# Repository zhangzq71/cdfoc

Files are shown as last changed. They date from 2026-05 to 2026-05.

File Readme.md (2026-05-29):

CDFOC Introduction
=======================================

Your browser may not support avif images!

Sockets: RS-485: molex 5264 (4 pin x 2), motor: molex 5264 (3 pin), sensor: sh1.0 (10 pin)

Download this project:
```
git clone --recursive https://github.com/dukelec/cdfoc
```



## Protocol

CDFOC is an open-source Field-Oriented Control (FOC) motor controller that communicates over an RS485 interface.
 - Default baud rate: 115200 bps
 - Maximum speed: 50 Mbps
 - Default address: 0xfe

The underlying protocol is CDBUS, with the following frame format:  
`src, dst, len, [payload], crc_l, crc_h`

Each frame includes a 3-byte header, a variable-length payload, and a 2-byte CRC (identical to Modbus CRC).  
For more information on the CDBUS protocol, please refer to:
 - https://cdbus.org

The payload is encoded using the CDNET protocol. For detailed information, please refer to:
 - https://github.com/dukelec/cdnet
 - https://github.com/dukelec/cdnet/wiki/CDNET-Intro-and-Demo

## Block Diagram



## GUI Tool

CDBUS GUI Tool: https://github.com/dukelec/cdbus_gui

Example: Upon power-on, first write 5 to `state`, then write the target position to `tp_pos` to rotate the motor.



After modifying the configuration, write 1 to `save_conf` to save the configuration to flash.  
If you need to restore the default configuration, change `magic_code` to another value and save it to flash. Then reapply power.

Plots:



## Operating

### Calibration mode (state = 1)

Do not connect any loads to the motor during calibration.

Write 1 to `dbg_en` to enable debug prints in the GUI.

Start by setting the appropriate value for `cali_current`, it is recommended to set the value a little higher to allow the motor to lock more accurately.
Also be careful to prevent the motor from overheating.

Write 1 to `cali_run` to start the calibration. The motor coils will be energized sequentially, causing the motor to turn clockwise first, then counterclockwise.
Afterward, the calculated encoder offset value will be printed and written to `bias_encoder`. Be sure to save it to flash.

Writing 1 to `cali_run` automatically sets `state` to 1.

### Torque Mode (state = 2)

Write 2 to `state` to enter torque mode, or current mode. 

The motor can then be rotated by writing the appropriate current value to `tgt_current`. 

The unit of current is the LSB value of the 12bits ADC. 

### Speed Mode (state = 3)

Write 3 to `state` to enter speed mode.

Then write the appropriate speed value to `tgt_speed` to rotate the motor.

One revolution of the motor is divided into 0x10000 units, e.g. from 0 to 0x10000 is one full revolution.  
The unit of speed is: how many position-units / second.

### Position Mode (state = 5)

Write 5 to `state` to enter position mode.

Then just write the appropriate values to `tp_pos`, `tp_speed`, `tp_accel`.

Alternatively these parameters can be updated using the quick-exchange command by default.

Mode 4 of `state` is a position mode without acceleration or deceleration and is not normally used.

## Command Demonstration

The address of the `state` itself is `0x0240` and its length is 1 byte.
To lock the motor and enter position mode after power up, send the following data to port 5:
```
20  40 02  05
```
`20` is the subcommand `write`, `40 02` is the little-endian for address 0x0240 (little-endian is used unless otherwise noted),
and `05` is the value to be written.

The complete command containing the CRC is (host address defaults to `0`, motor address defaults to `0xfe`, 3rd byte is data length, last two bytes are CRC):

```
00 fe 06  40 05  20  40 02  05  eb 8f
```

The complete response package is:
```
fe 00 03  05 40  00  crc_l crc_h
```

The last `0x00` means no error.

### Quick Exchange Commands

`qxchg_set` uses only one element by default, pointing to the area where the table entries `tp_pos`, `tp_speed` and `tp_accel` are located.  
If you want to change the target position parameter `tp_pos` to 0, you can write data `00 00 00 00` to port 6.  

If you need to change both the target position and the target speed, e.g. position to 0x00010000 and speed to 0x00005000, writes: `00 00 01 00  00 50 00 00`.

Goes to 0 degrees, full command with CRC:
```
00 fe 06  40 06  00 00 00 00  64 f8
```

Goes to 180 degrees, full command with CRC:  
(0x10000 units for one revolution, 0x8000 for 180 degrees)

```
00 fe 06  40 06  00 80 00 00  65 10
```

Rotates to the 5th revolution position and sends the speed value (0x00140000 or 14 revolutions per second) with the CRC:
```
00 fe 0a  40 06  00 00 05 00  00 00 14 00  ae c4
```

Demonstration of return data for the above three commands:
```
fe 00 0a  06 40  xx xx xx xx yy yy yy yy  crc_l crc_h
```

The `xx` and `yy` are defined by `qxchg_ret` to return 8 bytes of data such as `tgt_pos`.

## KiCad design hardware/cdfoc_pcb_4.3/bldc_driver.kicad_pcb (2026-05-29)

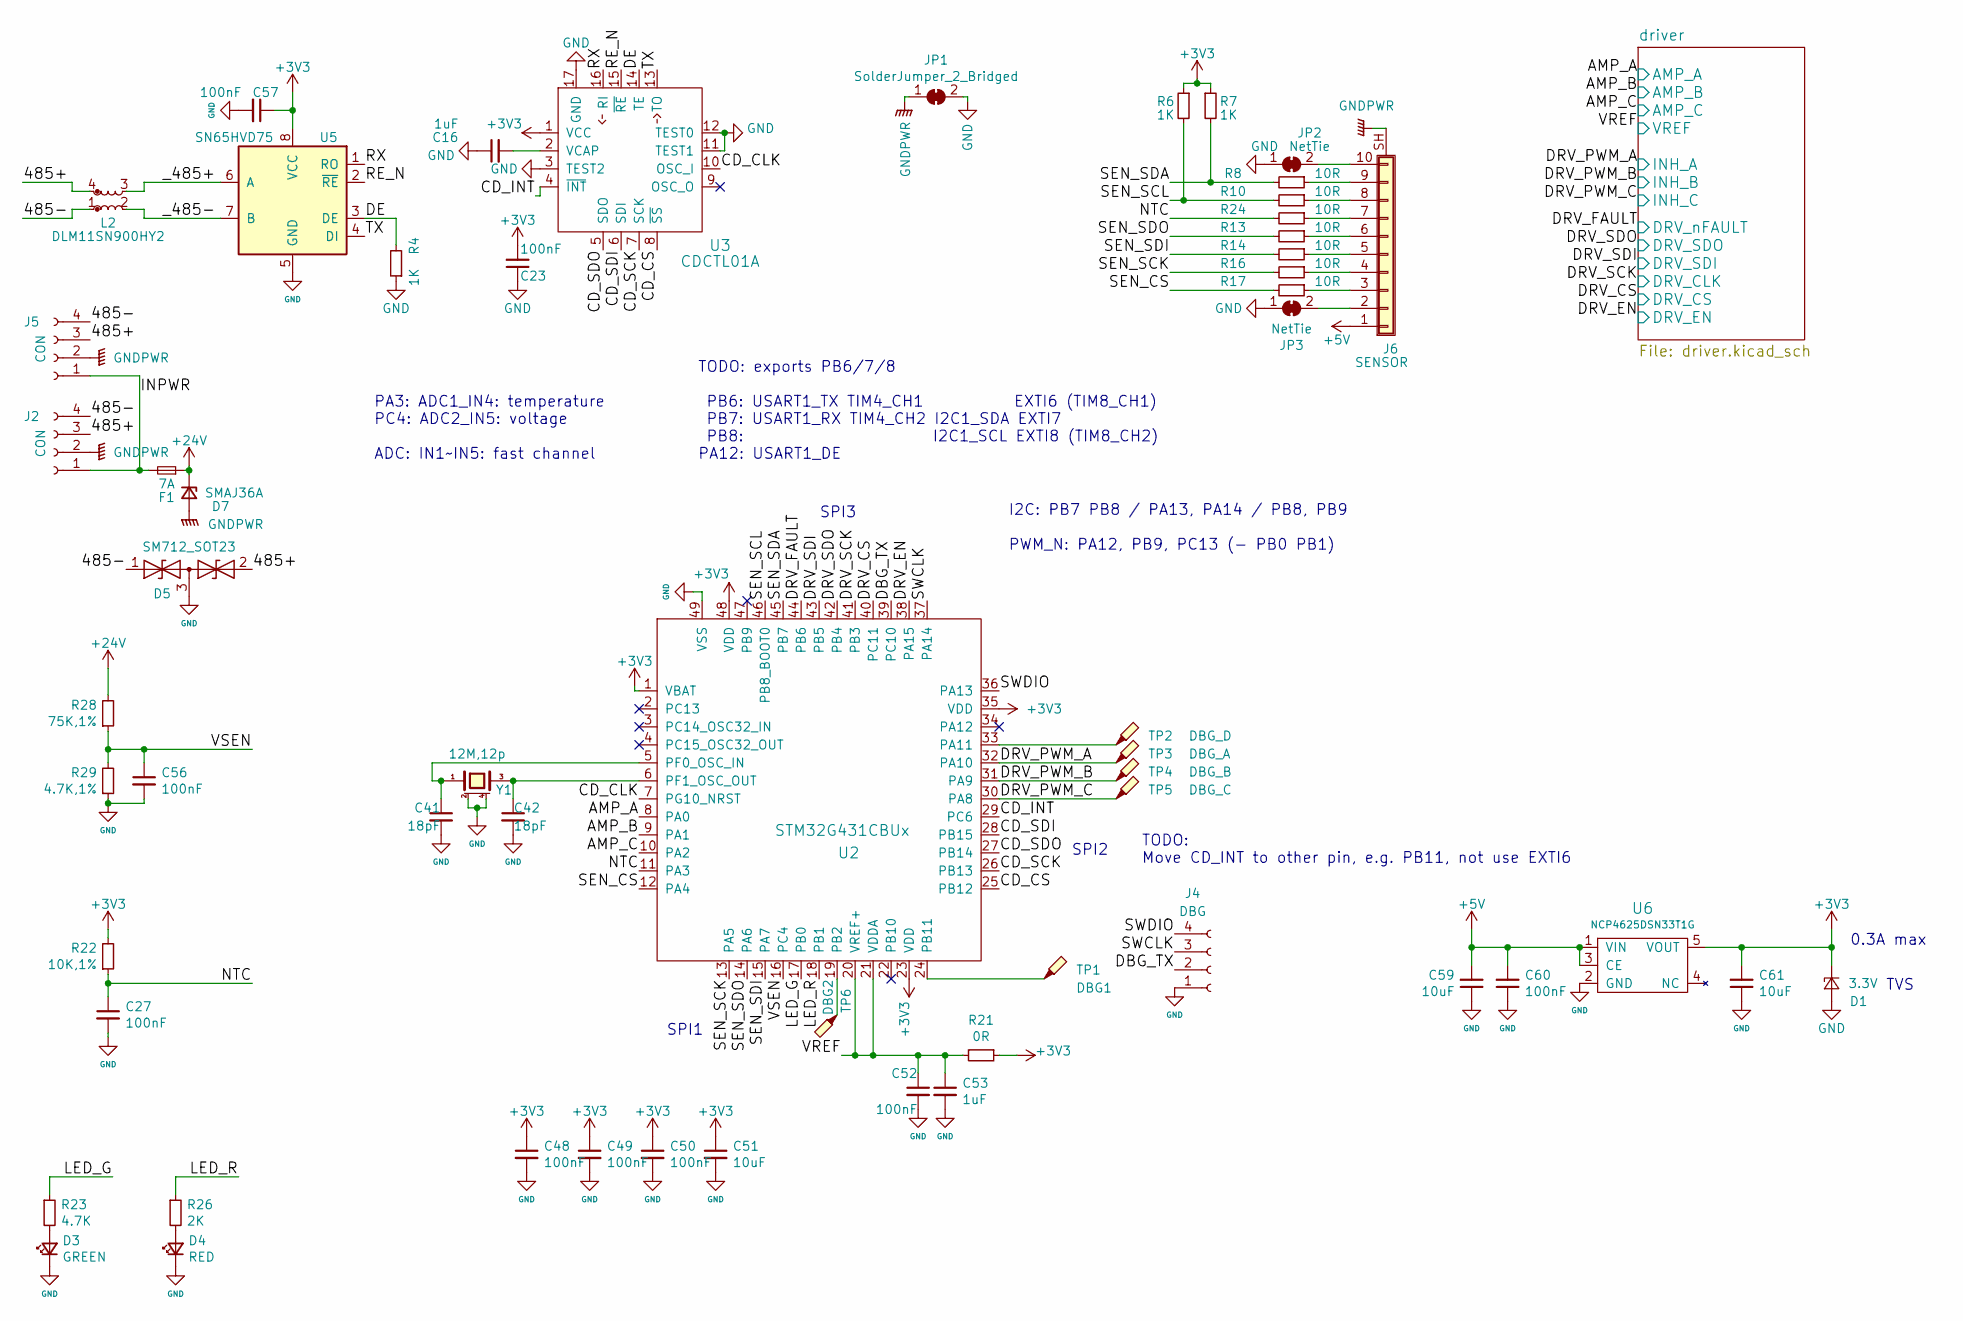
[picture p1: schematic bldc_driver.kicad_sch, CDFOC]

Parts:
C16, C53: 1uF; 0402
C23, C27, C48, C49, C50, C52, C56, C57, C60: 100nF; 0402
C41, C42: 18pF; 0402
C51, C59, C61: 10uF; 0402C_BIG
D1: 3.3V; SOD-923
D3: GREEN; 0402D
D4: RED; 0402D
D5: SM712_SOT23; SOT-23
D7: SMAJ36A; SMA
F1: 7A; 1206R
J2, J5: CON; CONN_5268-04A_1x04_P2.50mm_H
J4: DBG; PAD_DIP_4P_1mm
J6: SENSOR; CONN_SH1.0mm_10P_HSMD
JP1: SolderJumper_2_Bridged; NetTie-2_SMD_Pad1mm
JP2, JP3: NetTie; NetTie-2_SMD_Pad0.5mm
L2: DLM11SN900HY2; L_CommonModeChoke_Coilcraft_0603USB
R4, R6, R7: 1K; 0402
R8, R10, R13, R14, R16, R17, R24: 10R; 0402
R21: 0R; 0402
R22: 10K,1%; 0402
R23: 4.7K; 0402
R26: 2K; 0402
R28: 75K,1%; 0402
R29: 4.7K,1%; 0402
TP1: DBG1; TP-D0.8mm
TP2: DBG_D; TP-D0.8mm
TP3: DBG_A; TP-D0.8mm
TP4: DBG_B; TP-D0.8mm
TP5: DBG_C; TP-D0.8mm
TP6: DBG2; TP-D0.8mm
U2: STM32G431CBUx; QFN-48-1EP_7x7mm_P0.5mm_EP5.6x5.6mm
U3: CDCTL01A; QFN-16-1EP_3x3mm_P0.5mm_EP1.7x1.7mm
U5: SN65HVD75; SON-8
U6: NCP4625DSN33T1G; SOT-23-5
Y1: 12M,12p; XTAL-3225

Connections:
+3V3: C23.2, C48.1, C49.1, C50.1, C51.1, C57.1, C61.2, D1.1 (K), R6.1, R7.1, R21.1, R22.2, U2.1 (VBAT), U2.23 (VDD), U2.35 (VDD), U2.48 (VDD), U3.1 (VCC), U5.8 (VCC), U6.5 (VOUT); also elsewhere on the board
+5V: C59.2, C60.2, J6.1, U6.1 (VIN), U6.3 (CE); also elsewhere on the board
+24V: D7.1 (K), F1.1, R28.2; also elsewhere on the board
/485+: D5.2 (A2), J2.3, J5.3, L2.4
/485-: D5.1 (A1), J2.4, J5.4, L2.1
/AMP_A: U2.8 (PA0); also elsewhere on the board
/AMP_B: U2.9 (PA1); also elsewhere on the board
/AMP_C: U2.10 (PA2); also elsewhere on the board
/CD_CLK: U2.7 (PG10_NRST), U3.10 (OSC_I)
/CD_CS: U2.25 (PB12), U3.8 (~SS)
/CD_INT: U2.29 (PC6), U3.4 (~INT)
/CD_SCK: U2.26 (PB13), U3.7 (SCK)
/CD_SDI: U2.28 (PB15), U3.6 (SDI)
/CD_SDO: U2.27 (PB14), U3.5 (SDO)
/DBG_TX: J4.2, U2.39 (PC10)
/DE: R4.2, U3.14 (TE), U5.3 (DE)
/DRV_CS: U2.40 (PC11); also elsewhere on the board
/DRV_EN: U2.38 (PA15); also elsewhere on the board
/DRV_FAULT: U2.44 (PB6); also elsewhere on the board
/DRV_PWM_A: TP3.1, U2.32 (PA10); also elsewhere on the board
/DRV_PWM_B: TP4.1, U2.31 (PA9); also elsewhere on the board
/DRV_PWM_C: TP5.1, U2.30 (PA8); also elsewhere on the board
/DRV_SCK: U2.41 (PB3); also elsewhere on the board
/DRV_SDI: U2.43 (PB5); also elsewhere on the board
/DRV_SDO: U2.42 (PB4); also elsewhere on the board
/INPWR: F1.2, J2.1, J5.1
/LED_G: R23.1, U2.17 (PB0)
/LED_R: R26.1, U2.18 (PB1)
/NTC: C27.1, R22.1, R24.2, U2.11 (PA3)
/RE_N: U3.15 (~RE), U5.2 (~RE)
/RX: U3.16 (RI), U5.1 (RO)
/SEN_CS: R17.2, U2.12 (PA4)
/SEN_SCK: R16.2, U2.13 (PA5)
/SEN_SCL: R6.2, R10.2, U2.46 (PB8_BOOT0)
/SEN_SDA: R7.2, R8.2, U2.45 (PB7)
/SEN_SDI: R14.2, U2.15 (PA7)
/SEN_SDO: R13.2, U2.14 (PA6)
/SWCLK: J4.3, U2.37 (PA14)
/SWDIO: J4.4, U2.36 (PA13)
/TX: U3.13 (TO), U5.4 (DI)
/VREF: C52.1, C53.1, R21.2, U2.20 (VREF+), U2.21 (VDDA); also elsewhere on the board
/VSEN: C56.1, R28.1, R29.2, U2.16 (PC4)
/_485+: L2.3, U5.6 (A)
/_485-: L2.2, U5.7 (B)
GND: C16.1, C23.1, C27.2, C41.2, C42.2, C48.2, C49.2, C50.2, C51.2, C52.2, C53.2, C56.2, C57.2, C59.1, C60.1, C61.1, D1.2 (A), D3.1 (K), D4.1 (K), D5.3 (common), J4.1, JP1.2 (B), JP2.1 (A), JP3.1 (A), R4.1, R29.1, U2.49 (VSS), U3.3 (TEST2), U3.11 (TEST1), U3.12 (TEST0), U3.17 (GND), U5.5 (GND), U6.2 (GND), Y1.2 (case), Y1.4 (case); also elsewhere on the board
GNDPWR: D7.2 (A), J2.2, J5.2, J6.SH (Shield), JP1.1 (A); also elsewhere on the board
unnamed: D3.2 (A), R23.2
unnamed: D4.2 (A), R26.2
unnamed: J6.2, JP3.2 (B)
unnamed: J6.3, R17.1
unnamed: J6.4, R16.1
unnamed: J6.5, R14.1
unnamed: J6.6, R13.1
unnamed: J6.7, R24.1
unnamed: J6.8, R10.1
unnamed: J6.9, R8.1
unnamed: J6.10, JP2.2 (B)
unnamed: TP2.1, U2.33 (PA11)
unnamed: TP6.1, U2.19 (PB2)
unnamed: TP1.1, U2.24 (PB11)
unnamed: C41.1, U2.5 (PF0_OSC_IN), Y1.1
unnamed: C42.1, U2.6 (PF1_OSC_OUT), Y1.3
unnamed: C16.2, U3.2 (VCAP)

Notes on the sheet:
PA3: ADC1_IN4: temperature PC4: ADC2_IN5: voltage ADC: IN1~IN5: fast channel
TODO: Move CD_INT to other pin, e.g. PB11, not use EXTI6
TODO: exports PB6/7/8 PB6: USART1_TX TIM4_CH1 EXTI6 (TIM8_CH1) PB7: USART1_RX TIM4_CH2 I2C1_SDA EXTI7 PB8: I2C1_SCL EXTI8 (TIM8_CH2) PA12: USART1_DE
SPI3
SPI1
TVS
I2C: PB7 PB8 / PA13, PA14 / PB8, PB9 PWM_N: PA12, PB9, PC13 (- PB0 PB1)
0.3A max
SPI2

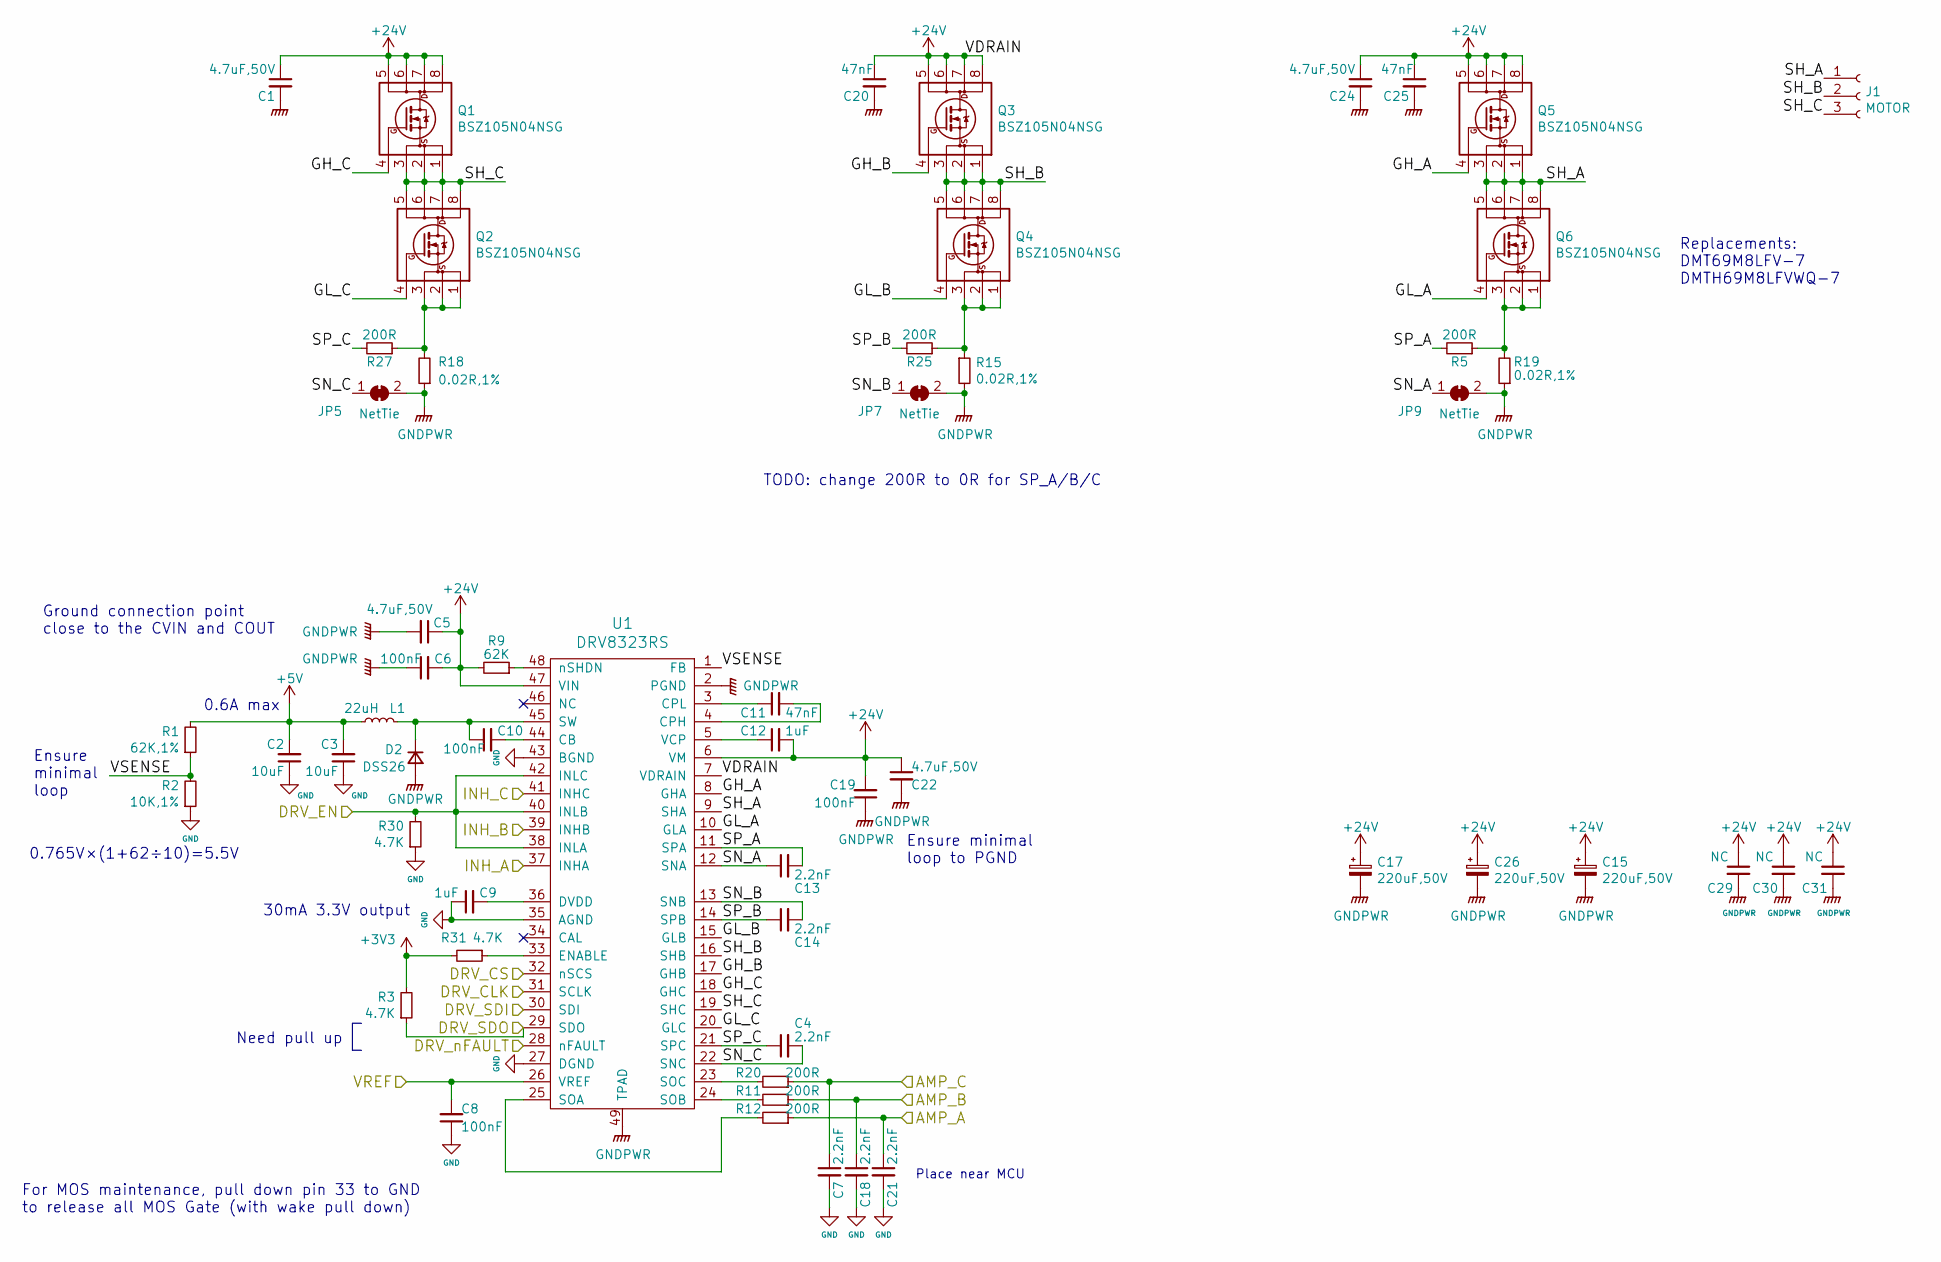
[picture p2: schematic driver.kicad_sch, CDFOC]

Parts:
C1, C5, C22, C24: 4.7uF,50V; 0805
C2, C3: 10uF; 0402C_BIG
C4, C7, C13, C14, C18, C21: 2.2nF; 0402
C6, C8, C10, C19: 100nF; 0402
C9, C12: 1uF; 0402
C11, C20, C25: 47nF; 0402
C15, C17, C26: 220uF,50V; CP_Elec_10x10
C29, C30, C31: NC; 1206
D2: DSS26; D_SOD-123F
J1: MOTOR; CONN_5268-03A_1x03_P2.50mm_H
JP5, JP7, JP9: NetTie; NetTie-2_SMD_Pad0.16mm
L1: 22uH; L_Taiyo-Yuden_MD-4040
Q1, Q2, Q3, Q4, Q5, Q6: BSZ105N04NSG; PG-TSDSON-8_3x3mm
R1: 62K,1%; 0402
R2: 10K,1%; 0402
R3, R30, R31: 4.7K; 0402
R5, R11, R12, R20, R25, R27: 200R; 0402
R9: 62K; 0402
R15, R18, R19: 0.02R,1%; 1206R
U1: DRV8323RS; QFN-48-1EP_7x7mm_P0.5mm_EP5.15x5.15mm

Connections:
+3V3: R3.2, R31.2; also elsewhere on the board
+5V: C2.2, C3.2, L1.1, R1.2; also elsewhere on the board
+24V: C1.1, C5.1, C6.2, C12.2, C15.1, C17.1, C19.2, C20.1, C22.1, C24.1, C25.1, C26.1, C29.1, C30.1, C31.1, Q1.5 (D), Q1.6 (D), Q1.7 (D), Q1.8 (D), Q3.5 (D), Q3.6 (D), Q3.7 (D), Q3.8 (D), Q5.5 (D), Q5.6 (D), Q5.7 (D), Q5.8 (D), R9.2, U1.6 (VM), U1.7 (VDRAIN), U1.47 (VIN); also elsewhere on the board
/AMP_A: C21.1, R12.1; also elsewhere on the board
/AMP_B: C18.1, R11.1; also elsewhere on the board
/AMP_C: C7.1, R20.1; also elsewhere on the board
/DRV_CS: U1.32 (nSCS); also elsewhere on the board
/DRV_EN: R30.2, U1.38 (INLA), U1.40 (INLB), U1.42 (INLC); also elsewhere on the board
/DRV_FAULT: U1.28 (nFAULT); also elsewhere on the board
/DRV_PWM_A: U1.37 (INHA); also elsewhere on the board
/DRV_PWM_B: U1.39 (INHB); also elsewhere on the board
/DRV_PWM_C: U1.41 (INHC); also elsewhere on the board
/DRV_SCK: U1.31 (SCLK); also elsewhere on the board
/DRV_SDI: U1.30 (SDI); also elsewhere on the board
/DRV_SDO: R3.1, U1.29 (SDO); also elsewhere on the board
/VREF: C8.2, U1.26 (VREF); also elsewhere on the board
/driver/GH_A: Q5.4 (G), U1.8 (GHA)
/driver/GH_B: Q3.4 (G), U1.17 (GHB)
/driver/GH_C: Q1.4 (G), U1.18 (GHC)
/driver/GL_A: Q6.4 (G), U1.10 (GLA)
/driver/GL_B: Q4.4 (G), U1.15 (GLB)
/driver/GL_C: Q2.4 (G), U1.20 (GLC)
/driver/SH_A: J1.1, Q5.1 (S), Q5.2 (S), Q5.3 (S), Q6.5 (D), Q6.6 (D), Q6.7 (D), Q6.8 (D), U1.9 (SHA)
/driver/SH_B: J1.2, Q3.1 (S), Q3.2 (S), Q3.3 (S), Q4.5 (D), Q4.6 (D), Q4.7 (D), Q4.8 (D), U1.16 (SHB)
/driver/SH_C: J1.3, Q1.1 (S), Q1.2 (S), Q1.3 (S), Q2.5 (D), Q2.6 (D), Q2.7 (D), Q2.8 (D), U1.19 (SHC)
/driver/SN_A: C13.1, JP9.1 (A), U1.12 (SNA)
/driver/SN_B: C14.2, JP7.1 (A), U1.13 (SNB)
/driver/SN_C: C4.2, JP5.1 (A), U1.22 (SNC)
/driver/SP_A: C13.2, R5.2, U1.11 (SPA)
/driver/SP_B: C14.1, R25.2, U1.14 (SPB)
/driver/SP_C: C4.1, R27.2, U1.21 (SPC)
/driver/VSENSE: R1.1, R2.2, U1.1 (FB)
GND: C2.1, C3.1, C7.2, C8.1, C9.1, C18.2, C21.2, R2.1, R30.1, U1.27 (DGND), U1.35 (AGND), U1.43 (BGND); also elsewhere on the board
GNDPWR: C1.2, C5.2, C6.1, C15.2, C17.2, C19.1, C20.2, C22.2, C24.2, C25.2, C26.2, C29.2, C30.2, C31.2, D2.2 (A), JP5.2 (B), JP7.2 (B), JP9.2 (B), R15.2, R18.1, R19.1, U1.2 (PGND), U1.49 (TPAD); also elsewhere on the board
unnamed: C10.1, D2.1 (K), L1.2, U1.45 (SW)
unnamed: Q2.1 (S), Q2.2 (S), Q2.3 (S), R18.2, R27.1
unnamed: Q4.1 (S), Q4.2 (S), Q4.3 (S), R15.1, R25.1
unnamed: Q6.1 (S), Q6.2 (S), Q6.3 (S), R5.1, R19.2
unnamed: C10.2, U1.44 (CB)
unnamed: C11.2, U1.4 (CPH)
unnamed: C11.1, U1.3 (CPL)
unnamed: C9.2, U1.36 (DVDD)
unnamed: R31.1, U1.33 (ENABLE)
unnamed: R12.2, U1.25 (SOA)
unnamed: R11.2, U1.24 (SOB)
unnamed: R20.2, U1.23 (SOC)
unnamed: C12.1, U1.5 (VCP)
unnamed: R9.1, U1.48 (nSHDN)

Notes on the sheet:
Ground connection point close to the CVIN and COUT
Need pull up
For MOS maintenance, pull down pin 33 to GND to release all MOS Gate (with wake pull down)
Replacements: DMT69M8LFV-7 DMTH69M8LFVWQ-7
30mA 3.3V output
Ensure minimal loop to PGND
TODO: change 200R to 0R for SP_A/B/C
0.765V×(1+62÷10)=5.5V
0.6A max
Place near MCU
Ensure minimal loop

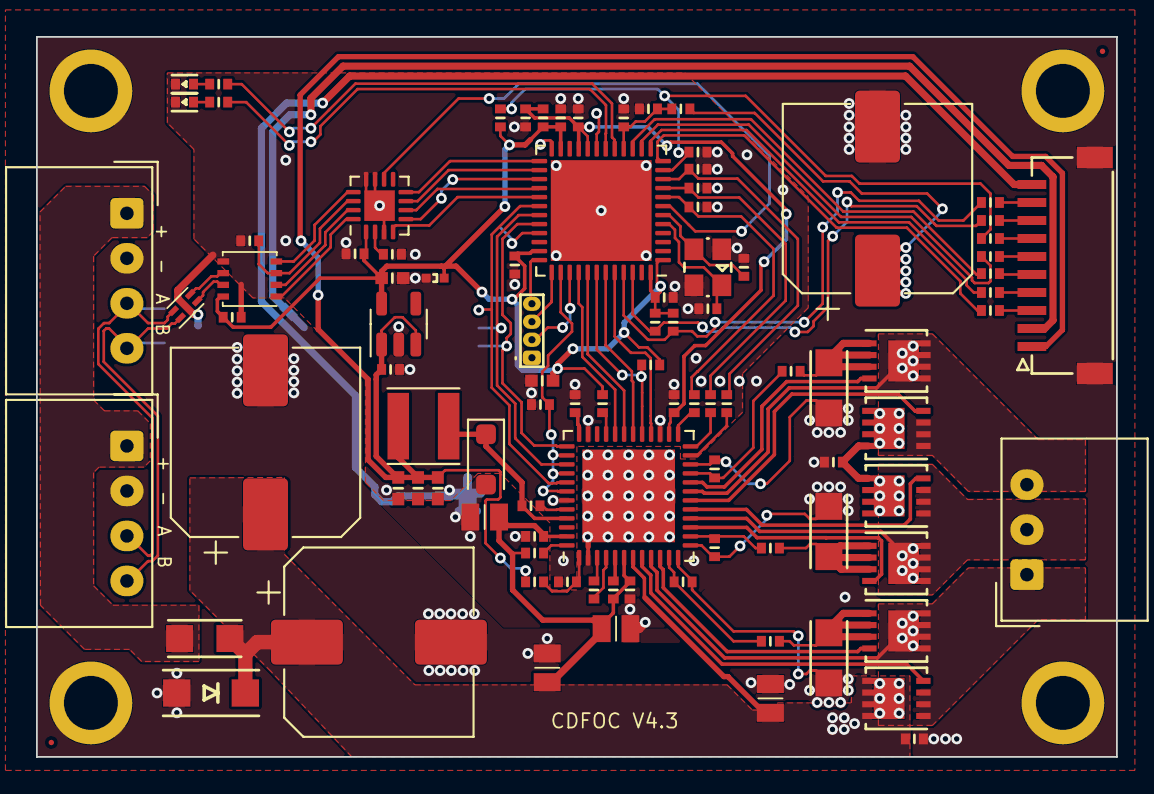
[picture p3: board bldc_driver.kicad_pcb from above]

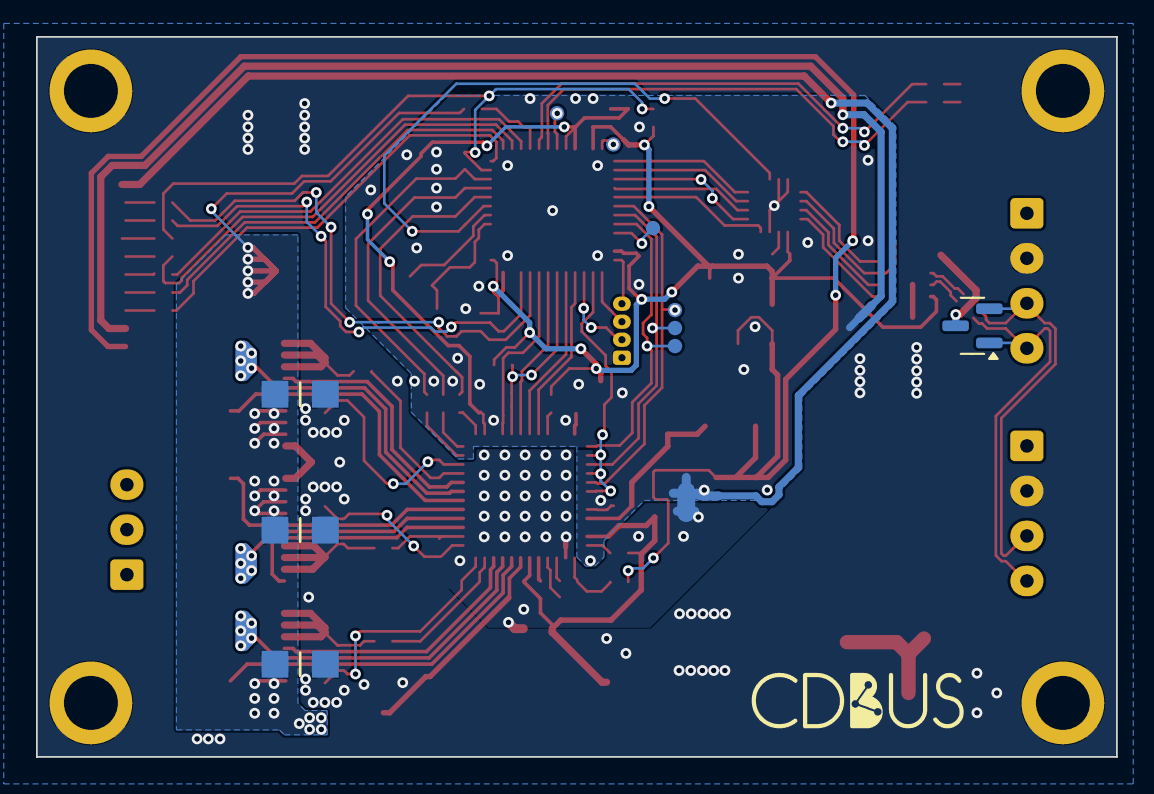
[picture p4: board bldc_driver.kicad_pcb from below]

Board: 2 copper layers, 60.0 x 40.0 mm, 116 parts (13 on the bottom side), 93 nets.

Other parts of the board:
J11, J12, J13, J14: Hole; Hole-TH-3.2mm_4mm

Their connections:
GNDPWR: J11.1, J12.1, J13.1, J14.1; also elsewhere on the board

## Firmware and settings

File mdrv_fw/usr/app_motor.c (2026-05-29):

/*
 * Software License Agreement (MIT License)
 *
 * Copyright (c) 2017, DUKELEC, Inc.
 * All rights reserved.
 *
 * Author: Duke Fong <d@d-l.io>
 */

#include <math.h>
#include "app_main.h"

static adc_samp_t adc_samp = {0};
static encoder_filter_t enc_filter = {0};

static encoder_linearizer_t enc_lin = {
        .lut = (int8_t *)ENC_LIN_TBL
};

static anticog_t anticog = {
        .lut = (int8_t *)ANTICOG_TBL
};

static trap_planner_t trap_planner = {
        .dt = 25.0f / CURRENT_LOOP_FREQ
};

static int vector_over_limit = 0;
static uint8_t pos_loop_cnt = 0;
static uint8_t speed_loop_cnt = 0;
static float tgt_speed_bk = 0;
static int32_t tgt_current_bk = 0;


uint8_t state_w_hook_before(uint16_t sub_offset, uint8_t len, uint8_t *dat)
{
    if (*dat == ST_STOP) {
        gpio_set_val(&drv_en, 0);
        gpio_set_val(&led_r, 0);
        csa.adc_sel = 0;

    } else if (csa.state == ST_STOP && *dat != ST_STOP) {
        gpio_set_val(&drv_en, 1);
        csa.adc_sel = 0;
        delay_systick(50);

        d_debug("drv 05: %04x\n", drv_read_reg(0x05)); // default 0x0159, 100ns dead time
        d_debug("drv 03: %04x\n", drv_read_reg(0x03)); // default 0x03ff
        d_debug("drv 04: %04x\n", drv_read_reg(0x04)); // default 0x07ff
        drv_write_reg(0x03, 0x0388); // 260mA, 520mA
        drv_write_reg(0x04, 0x0788); // 260mA, 520mA
        d_debug("drv 03: %04x\n", drv_read_reg(0x03));
        d_debug("drv 04: %04x\n", drv_read_reg(0x04));

        d_debug("drv 02: %04x\n", drv_read_reg(0x02)); // default 0x0000
        drv_write_reg(0x02, 0x1 << 2); // COAST mode
        d_debug("drv 02: %04x\n", drv_read_reg(0x02));

        delay_systick(5);
        d_debug("drv 06: %04x\n", drv_read_reg(0x06)); // default 0x0283
        drv_write_reg(0x06, 0x0283 | (7 << 2)); // cali amplifier
        d_debug("drv 06: %04x\n", drv_read_reg(0x06));
        delay_systick(5);
        drv_write_reg(0x06, 0x0283);
        d_debug("drv 06: %04x\n", drv_read_reg(0x06));
        delay_systick(5);

        adc_samp_cali(&adc_samp);

        drv_write_reg(0x02, (1 << 7) | (1 << 5)); // otw err, 3x pwm mode
        d_debug("drv 02: %04x\n", drv_read_reg(0x02));
    }
    return 0;
}

uint8_t motor_w_hook_after(uint16_t sub_offset, uint8_t len, uint8_t *dat)
{
    uint32_t flags;

    if (csa.state == ST_POS_TP) {
        local_irq_save(flags);
        if (csa.tgt_pos != csa.tp_pos)
            trap_planner.state = 1; // restart t_curve
        local_irq_restore(flags);
    }
    return 0;
}


void app_motor_init(void)
{
    pid_f_reset(&csa.pid_i_sq, 0);
    pid_f_reset(&csa.pid_i_sd, 0);
    pid_f_reset(&csa.pid_speed, 0);
    pid_i_reset(&csa.pid_pos, 0);
    csa.bus_voltage = csa.nominal_voltage;
    csa2encoder_linearizer_mt(&enc_lin);
    csa2anticog_mt(&anticog);
}

void app_motor_maintain(void)
{
    static uint32_t t_last = 0;
    if (vector_over_limit && (t_last == 0 || get_systick() - t_last > 500)) {
        d_debug("!~!~ %d ~!~!\n", vector_over_limit);
        vector_over_limit = 0;
        t_last = get_systick();
    }

    csa2encoder_filter_mt(&enc_filter);
    csa2trap_planner_mt(&trap_planner);

    if (adc_samp.has_new_regular) {
        int16_t adc_dc = adc_samp.regular_i[1];
        int16_t adc_temp = adc_samp.regular_i[0];

        float v_dc = (adc_dc / 4095.0f * 3.3f) / 4.7f * (4.7f + 75);
        csa.bus_voltage += (v_dc - csa.bus_voltage) * 0.05f;

        //    pull-up: 10K
        float r_ntc = (10000.0f * adc_temp) / (4095 - adc_temp);
        float temp = (1.0f / ((1.0f / csa.ntc_b) * logf(r_ntc / csa.ntc_r25) + (1.0f / (25 + 273.15f))) - 273.15f);
        csa.motor_temp += (temp - csa.motor_temp) * 0.02f;
        adc_samp.has_new_regular = false;

        if (csa.motor_temp > csa.temp_err) {
            csa.err_flag_.motor_otsd = 1;
            state_w_hook_before(0, 0, (uint8_t []){ST_STOP});
            csa.state = ST_STOP;
        } else if (csa.motor_temp > csa.temp_warn) {
            csa.err_flag_.motor_otw = 1;
        }
        if (csa.bus_voltage < csa.voltage_min)
            csa.err_flag_.motor_uvlo = 1;
        if (csa.bus_voltage > csa.voltage_max)
            csa.err_flag_.motor_ovlo = 1;
    }
}


static inline void position_loop_update(void)
{
    if (++pos_loop_cnt < 5)
        return;
    pos_loop_cnt = 0;

    if (csa.state != ST_POS_TP) {
        trap_planner_reset(&trap_planner, csa.meas_pos, csa.meas_speed_avg);
        trap_planner2csa_rst(&trap_planner);
    } else {
        csa2trap_planner(&trap_planner);
        trap_planner_update(&trap_planner, csa.meas_pos);
        trap_planner2csa(&trap_planner);
    }

    if (csa.state < ST_POSITION) {
        //pid_i_reset(&csa.pid_pos, csa.meas_speed_avg);
        pid_i_set_target(&csa.pid_pos, csa.meas_pos);
        csa.tgt_pos = csa.meas_pos;
        tgt_speed_bk = csa.meas_speed_avg;
        if (csa.state == ST_STOP) {
            csa.tgt_speed = 0;
            tgt_speed_bk = 0;
        }
    } else {
        pid_i_set_target(&csa.pid_pos, csa.tgt_pos);
        tgt_speed_bk = csa.tgt_speed;
        csa.tgt_speed = pid_i_update_p_only(&csa.pid_pos, csa.meas_pos);
        if (csa.state == ST_POS_TP)
            csa.tgt_speed += csa.tp_vel_out;
    }

    raw_dbg(2);
    raw_dbg(3);
}


static inline void speed_loop_update(void)
{
    if (++speed_loop_cnt < 5)
        return;
    speed_loop_cnt = 0;
    position_loop_update();

    if (csa.state < ST_SPEED) {
        pid_f_reset(&csa.pid_speed, csa.tgt_current);
        pid_f_set_target(&csa.pid_speed, csa.meas_speed_avg);
        csa.tgt_speed = csa.meas_speed_avg;
        if (csa.state == ST_STOP) {
            csa.tgt_current = 0;
            csa.tgt_speed = 0;
            tgt_speed_bk = 0;
        }
        tgt_current_bk = csa.tgt_current;
    } else {
        if (csa.state == ST_SPEED) {
            float v_step = (float)csa.tp_accel / (CURRENT_LOOP_FREQ / 5.0f);
            float speed = csa.pid_speed.target <= csa.tgt_speed ?
                    min(csa.pid_speed.target + v_step, csa.tgt_speed) : max(csa.pid_speed.target - v_step, csa.tgt_speed);
            pid_f_set_target(&csa.pid_speed, speed);
        } else {
            float speed = tgt_speed_bk + (csa.tgt_speed - tgt_speed_bk) / 5 * (pos_loop_cnt + 1);
            pid_f_set_target(&csa.pid_speed, speed);
        }
        tgt_current_bk = csa.tgt_current;
        csa.tgt_current = lroundf(pid_f_update(&csa.pid_speed, csa.meas_speed_avg, csa.meas_speed));
    }

    raw_dbg(1);
}
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

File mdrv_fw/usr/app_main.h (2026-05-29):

/*
 * Software License Agreement (MIT License)
 *
 * Copyright (c) 2017, DUKELEC, Inc.
 * All rights reserved.
 *
 * Author: Duke Fong <d@d-l.io>
 */

#ifndef __APP_MAIN_H__
#define __APP_MAIN_H__

#include <math.h>
#include "cdnet_core.h"
#include "cd_debug.h"
#include "cdbus_uart.h"
#include "cdctl_it.h"
#include "pid_f.h"
#include "pid_i.h"

// printf float value without enable "-u _printf_float"
// e.g.: printf("%d.%.2d\n", P_2F(2.14));
#define P_2F(x) (int)(x), abs((int)(((x)-(int)(x))*100))  // "%d.%.2d"
#define P_3F(x) (int)(x), abs((int)(((x)-(int)(x))*1000)) // "%d.%.3d"
#define M_PIf   ((float)M_PI)


#define BL_ARGS             0x20000000 // first word
#define ENC_LIN_TBL         0x0801d800 // 4k
#define ANTICOG_TBL         0x0801e800 // 4k
#define APP_CONF_ADDR       0x0801f800 // page 63, the last page
#define APP_CONF_VER        0x0201

#define CURRENT_LOOP_FREQ   (170000000.f / (4096 * 2))
#define DRV_PWM_HALF        2048

#define FRAME_MAX           60
#define PACKET_MAX          60


typedef enum {
    ST_STOP = 0,
    ST_CALI,
    ST_CURRENT,
    ST_SPEED,
    ST_POSITION,
    ST_POS_TP
} state_t;

typedef struct {
    uint16_t        offset;
    uint8_t         size;
} regr_t; // reg range

typedef struct {
    uint16_t        offset;
    uint16_t        size;
} reg2r_t; // reg range


typedef struct {
    uint16_t        magic_code;     // 0xcdcd
    uint16_t        conf_ver;
    uint8_t         conf_from;      // 0: default, 1: all from flash, 2: partly from flash
    uint8_t         do_reboot;
    bool            _reserved_bl;   // keep_in_bl for bl
    bool            save_conf;

    uint8_t         _bus_net;
    cdctl_cfg_t     bus_cfg;
    bool            dbg_en;
    uint8_t         _reserved0[6];
    #define         _end_common pid_pos

    pid_i_t         pid_pos;
    uint32_t        _reserved01[9];
    pid_f_t         pid_speed;
    uint32_t        _reserved02[9];
    pid_f_t         pid_i_sq;
    uint32_t        _reserved03[9];
    pid_f_t         pid_i_sd;
    uint32_t        _reserved04[9];

    float           peak_cur_threshold;
    int32_t         peak_cur_duration;

    uint8_t         motor_poles;
    bool            motor_wire_swap;
    uint16_t        bias_encoder;
    int32_t         bias_pos;

    regr_t          qxchg_mcast;     // for multicast
    regr_t          qxchg_set[5];
    regr_t          qxchg_ret[5];
    uint8_t         _reserved1[20];

    uint8_t         dbg_str_msk;    // bit0: dump_hw_status

    uint8_t         _reserved2[9];
    uint8_t         dbg_raw_msk;
    uint8_t         _reserved21;
    regr_t          dbg_raw[4][6];  // for: cur, speed, pos, trap_planner

    int32_t         tp_pos;
    uint32_t        tp_speed;
    uint32_t        tp_accel;

    uint8_t         _reserved3[8];

    float           cali_angle_elec;
    float           cali_current;
    float           cali_angle_speed_tgt; // target speed [rad/s]
    uint8_t         cali_run;

    bool            enc_linear_en;
    int16_t         enc_linear_max;
    bool            anticog_en;
    int16_t         anticog_max_iq;
    int16_t         anticog_ratio_vq;

    float           nominal_voltage;
    uint16_t        tp_max_err;
    uint16_t        ntc_b;
    uint32_t        ntc_r25; // ntc resistor @ 25°C
    uint8_t         temp_warn;
    uint8_t         temp_err;
    uint8_t         voltage_min;
    uint8_t         voltage_max;
    uint8_t         _reserved4[12];

    // end of flash
    #define         _end_save state

    state_t         state;
    union {
        uint16_t err_flag;
        struct {
            uint16_t motor_otw     : 1; // [0]  motor overtemperature warning
            uint16_t motor_otsd    : 1; // [1]  motor overtemperature shutdown
            uint16_t motor_uvlo    : 1; // [2]  motor undervoltage
            uint16_t motor_ovlo    : 1; // [3]  motor overvoltage
            uint16_t               : 3; // [6:4]
            uint16_t drv_fault     : 1; // [7]  indicates any error listed below
            uint16_t drv_gdf       : 1; // [8]  gate drive fault
            uint16_t drv_otw       : 1; // [9]  overtemperature warning
            uint16_t drv_otsd      : 1; // [10] overtemperature shutdown
            uint16_t drv_uvlo      : 1; // [11] undervoltage lockout fault
            uint16_t drv_cpuv      : 1; // [12] charge pump undervoltage fault
            uint16_t drv_oc        : 1; // [13] sense amplifier overcurrent
            uint16_t drv_vds_ocp   : 1; // [14] vds monitor overcurrent fault
            uint16_t               : 1; // [15]
        } err_flag_;
    };

    int32_t         tgt_pos;
    float           tgt_speed;
    int32_t         tgt_current;
    float           tgt_v_sq;
    float           tgt_v_sd;

    uint16_t        ori_encoder;

    uint16_t        nob_encoder; // no bias
    int32_t         nob_pos;
    uint16_t        meas_encoder;
    float           meas_speed;
    int32_t         meas_pos;
    float           meas_speed_avg;
    float           meas_rpm_avg;

    float           meas_i_sq;
    float           meas_i_sd;
    float           meas_angle_elec;

    uint32_t        loop_cnt;
    int32_t         peak_cur_cnt;

    // for trap_planner
    int8_t          tp_state; // -1: disable, 0: idle, 1: planning
    float           tp_vel_out;
    float           tp_acc_brake;

    uint8_t         adc_sel;  // cur adc channel group

    int16_t         meas_i[3];
    int16_t         pwm_dbg0[3]; // before deadtime compensate
    int16_t         pwm_dbg1[3]; // after deadtime compensate
    int16_t         pwm_uvw[3];

    float           meas_i_sq_avg;
    float           tgt_v_sq_avg;
    uint8_t         _reserved5[8];
    float           bus_voltage;
    float           motor_temp;
    float           cali_angle_speed;

} csa_t; // config status area


typedef uint8_t (*hook_func_t)(uint16_t sub_offset, uint8_t len, uint8_t *dat);

typedef struct {
    reg2r_t         range;
    hook_func_t     before;
    hook_func_t     after;
} csa_hook_t;


extern csa_t csa;
extern const csa_t csa_dft;

extern reg2r_t csa_w_allow[]; // writable list
extern int csa_w_allow_num;

extern csa_hook_t csa_w_hook[];
extern int csa_w_hook_num;
extern csa_hook_t csa_r_hook[];
extern int csa_r_hook_num;

uint32_t eflash_read_id(spi_t *dev);
uint8_t eflash_read_status(spi_t *dev);
void eflash_read(spi_t *dev, uint32_t addr, int len, uint8_t *buf);
void eflash_write(spi_t *dev, uint32_t addr, int len, const uint8_t *buf);
void eflash_erase_chip(spi_t *dev);
void eflash_cmd(spi_t *dev, uint8_t cmd);

int flash_erase(uint32_t addr, uint32_t len);
int flash_write(uint32_t addr, uint32_t len, const uint8_t *buf);

void app_main(void);
void load_conf(void);
int save_conf(void);
void csa_list_show(void);

void comm_service_init(void);
void comm_service_poll(void);
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

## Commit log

2026-05-29 加入两个程序， python sine_wave_ctrl.py --dev COM37 --baud 30000000 --mode pos --amplitude 200000 --duration 0 --freq 1.0 --rate 500, python sine_wave_ctrl.py --dev COM37 --mode tp --rpm 100 --dir cw --dura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
2026-05-29 加入 speed 模式
2026-05-29 这个版本才正确
2026-05-29 add hw
    [bldc_driver.kicad_pcb, bldc_driver.kicad_sch, driver.kicad_sch]
